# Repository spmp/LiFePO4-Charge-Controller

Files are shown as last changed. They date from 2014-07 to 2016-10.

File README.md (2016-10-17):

LiFePO4 Charge Controller
=========================

This is a rolling project to create a fully automatic
_LiFePO4_ battery charger for my, and possibly other 
battery packs based on the HP Blade power supply ESP-120.

Principal of operation
----------------------
LiFePO4 batteries have a relativly simple charging profile:

 * Charge at constant current up to a set voltage, usually 3.65Volts per cell
 * Turn off charging and rest the batteries for a given time
 * If you must, float the batteries at 3.45Vpc
 
Thanks to the efforts of a German group the ESP-120 is well
documented with a known and stable voltage control from 30-53V
with positive voltage into a trim-pot pin and 53-63 with a slight
negative voltage to this pin. There is an inverse relationship
between voltage at the pot, and the supplies output voltage.
~5Vin=> 30Vout, 0Vin=>53Vout.

To operate as a charger two of these units are connected
in series. This is easy as the DC output is isolated from
the case. To achieve constant current charging, the voltage of the
supplies is brought up slowly by modifying (decreasing) Vin 
whilst monitoring the current until the desired current is reached.
Vin is decreased to maintain this constant current until There
setpoint is reached, at which point the PSU's are turned off.

The PSU's are protected by a very large external diode (75A, 200V).

The planned itterations are as follows, with each mature
and completed iteration being moved into its appropriate 
folder upon completion:

Repo layout
-----------
```
.
├── code            Charge controller logic
│   └── AVR-lib     General AVR libraries. Should be a submodule
│       └── lib
├── doc             Documents relating to the ESP-120/HP3KW
├── pcb             Output PCB files
└── schematic       Schematic
```

The code is written in C using [Kdevelop] and built using [avr-gcc].

The schematic and PCB layout are done in [Kicad]

Current Implimentation
----------------------
Photos to come

Iterations:
------------
1.  **Mark I: Proof of concept using onboard**

    - Construction on breadboard
    - Powered off the PSU power GND - 12V via an LM7805, so has common ground with Cycle Analyst
    - shunt and differential opamp via built in 10bit ADC for current measurement
    - 100:1 resistor divider via 10bit ADC for output voltage measurement
    - Output is a PWM based 'DAC' to a fet/transistor between two pot's setting max/min voltage.
    - Output/input via isolated serial interface.
  
2.  **Mark II: further improvements**
    - Impliment isolated I2C to PSU controllers for PSON and current measurement.
    - Check PSU current VS shunt current, once verified they are the same with similar reliability, discontinue use of shunt.
    - Impliment software usart for Rx only to recieve SOC etc. from the cycle analyst
    - Assess whether external DAC's and ADC's are nescesarry.
    - Likely that external ADC will be, so use it.
    - Investigate and impliment different charging strategies.
    - LCD?
    - BMS integration
  
3.  **Mark III: Close to Final** 
    - PCB based, on its own board. 
    - Use specialised AVR with CAN support
    - Similar codebase to MarkII, trying to remove interrupt driven routines
    - Safety/Failsafe etc. much more error checking.
    - Impliment CAN somehow

Currently half way through Iteration 2. Soon BMS integration will be required, and maybe we will do CAN bus things then too. Maybe port to STM32.

### Mark I: Proof of concept using onboard, Design considerations

Inputs:
-------
 **Current:** 
   Current will be measured using the shunt resistor on the PSU's PCB.
   It has a resistance of 0.0002Ohm, and will require a diffrential opamp
   in order to amplify the signal to the 5V range. There is already an opamp
   on the PCB that does this, and it may be sufficient to use this.
   
   One 10bit ADC channel on the micro will do this, preferebly with the 
   1.25V internal reference.
   
   With a maximum current of say 60A, the finest measurement we can make is:
     60/1024 = 59mA
   which is sufficient.
   
 **Output Voltage**
   Output volatage will be measured by another 10bit ADC channel via a 100k:1k 
   resistor divider network.
   Using the internal 1.25 voltage reference, this gives a maximum measurable voltage of
   125V with an accuracy of 0.122, again, more than sufficient!
   (DAC RC calculator)[http://sim.okawa-denshi.jp/en/PWMtool.php]
   
Outputs:
--------
 **Vin:**
   Volatage between power ground and a pad from a reomoved potentiometer needs to 
   be adjusted from ~5V to 0V.
   
   In this implimentation we will use PWM driving a fet to ground on from the 5V supply rail
   with the pot pin in the middle, and a 330nF cap to ground.
   
 **Serial:**
   Debugging and logging will be via serial
   
 **LED's and stuff:**
   - Blinking light (things alive)
   - Charging
   - Complete
   - State of charge bar graph for in the window 8)
   - Even better would be EL wire or tape on the exterior.

[Kdevelop]: https://www.kdevelop.org/
[avr-gcc]: http://www.nongnu.org/avr-libc/
[kicad]: http://kicad-pcb.org/

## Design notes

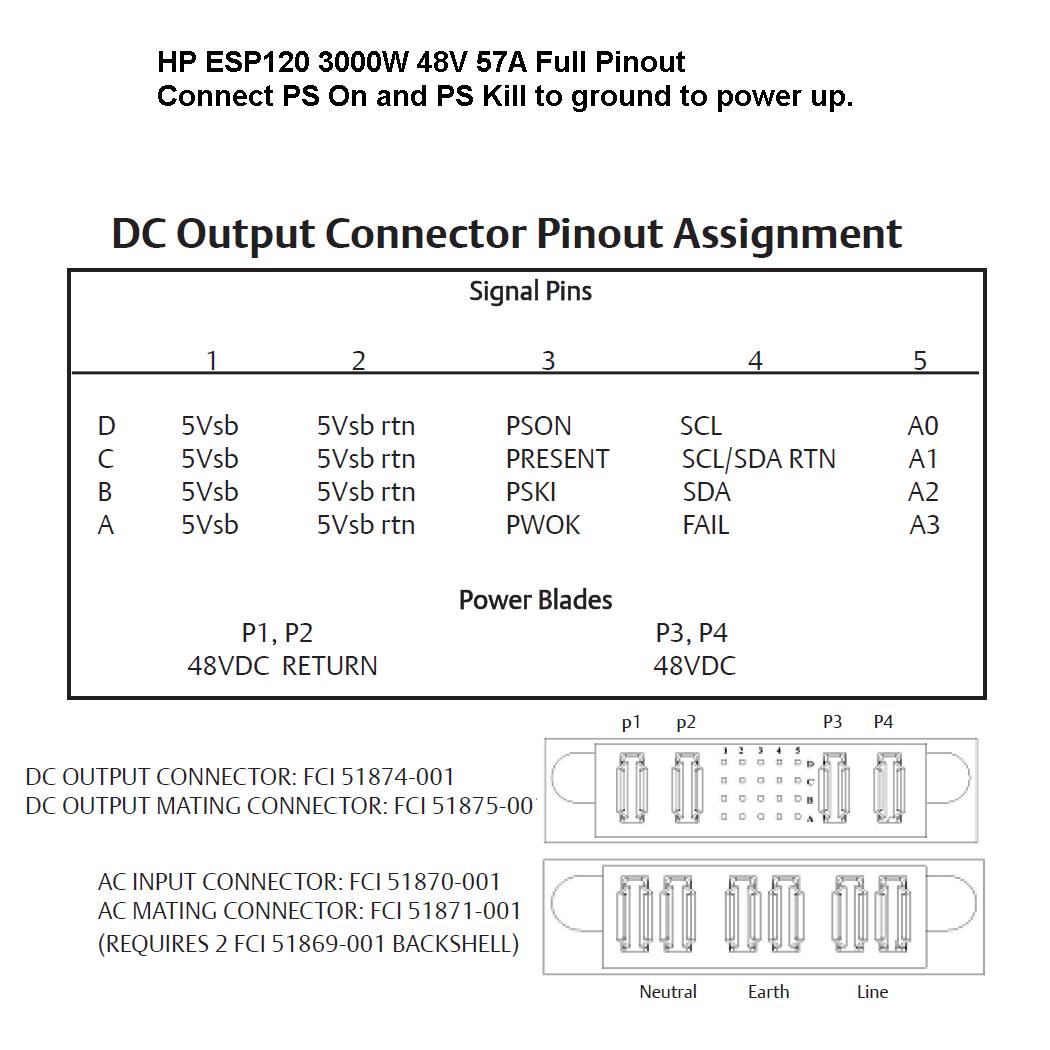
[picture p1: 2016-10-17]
doc/HP ESP120 Full pinout.jpg

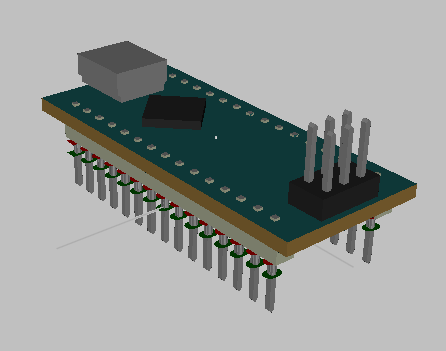
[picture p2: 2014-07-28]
schematic/arduino_nano.png

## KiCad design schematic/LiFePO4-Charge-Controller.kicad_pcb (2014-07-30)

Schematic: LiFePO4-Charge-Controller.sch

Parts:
CI1a1, CI1c1, CI2a1, CI2c1, CI3a1: 100nF
CI1b1, CI1d1, CI2b1, CI2d1, CI3b1: 1uF
CINA1: 100nF
CV1: 10pF
Cpwm1: 300nF
Dled1, Dled2: LED
OC1, OC2, OC3: PC817; DIP4
PI1, PI2, PI2C1: I2C
PIRS232: RS232
Popto1, Popto2, Popto3: opto
Pshunt1: differential
Pvolt1: Gnd PWM 12V B+
Qpnp1: NPN
RI1scl1, RI1sda1, RI2scl1, RI2sda1: 5k
RI2Cscl1, RI2Csda1: 1.8k
RVR1a1, RVR1b1: 99k
RVR2a1, RVR2b1: 1k
Rg1: 5k
Rled1: 1k
Rled2: 1K
Ropto1, Ropto2, Ropto3: 1k
Rpwm1: 120
RpwmDrv1: 560
UI1, UI2: SI8400; MODULE
UINA1: AD8236; MODULE
UIR1: SI8400; MODULE
UuC1: ARDUINO_Nano; DIL20

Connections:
5v: CI1a1.1, CI1b1.1, CI2a1.1, CI2b1.1, CI3a1.2, CI3b1.2, CINA1.1, PI2C1.1, RI2Cscl1.1, RI2Csda1.1, Rpwm1.2, UI1.8, UI2.8, UINA1.8 (+VS), UIR1.1, UuC1.12
D3: Ropto1.1, UuC1.21
D5: Ropto2.1, UuC1.23
D6: Ropto3.1, UuC1.24
Gnd: CI1a1.2, CI1b1.2, CI2a1.2, CI2b1.2, CI3a1.1, CI3b1.1, CINA1.2, CV1.2, Cpwm1.2, Dled1.2 (K), Dled2.2 (K), OC1.2, OC2.2, OC3.2, PI2C1.4, Pvolt1.4, Qpnp1.1 (E), RVR2a1.2, RVR2b1.2, UI1.5, UI2.5, UINA1.5 (-VS), UINA1.6 (REF), UIR1.4, UuC1.14, UuC1.19
I2C1_GND: CI1c1.2, CI1d1.2, PI1.4, UI1.4
I2C2_GND: CI2c1.2, CI2d1.2, PI2.4, UI2.4
unnamed: UIR1.2, UuC1.17
unnamed: UIR1.3, UuC1.16
unnamed: PI1.3, RI1scl1.2, UI1.3
unnamed: PI1.2, RI1sda1.2, UI1.2
unnamed: PI2.2, RI2sda1.2, UI2.2
unnamed: CV1.1, RVR1a1.2, RVR1b1.2, RVR2a1.1, RVR2b1.1, UuC1.4
unnamed: PIRS232.3, UIR1.6
unnamed: PIRS232.2, UIR1.7
unnamed: PIRS232.1, UIR1.8
unnamed: PI2.3, RI2scl1.2, UI2.3
unnamed: OC1.4, Popto1.1
unnamed: OC3.4, Popto3.1
unnamed: OC3.1, Ropto3.2
unnamed: OC2.3, Popto2.2 (PM)
unnamed: OC2.4, Popto2.1
unnamed: OC2.1, Ropto2.2
unnamed: OC1.3, Popto1.2 (PM)
unnamed: OC3.3, Popto3.2 (PM)
unnamed: OC1.1, Ropto1.2
unnamed: Cpwm1.1, Pvolt1.3, Qpnp1.3 (C), Rpwm1.1
unnamed: Qpnp1.2 (B), RpwmDrv1.2
unnamed: Dled1.1 (A), Rled1.2
unnamed: Dled2.1 (A), Rled2.2
unnamed: RpwmDrv1.1, UuC1.27
unnamed: Rled2.1, UuC1.30
unnamed: Rled1.1, UuC1.29
unnamed: Rg1.1, Rg1.2, UINA1.2 (RG)
unnamed: UINA1.7 (Vout), UuC1.5
unnamed: Pshunt1.2 (PM), UINA1.4 (+IN)
unnamed: Pshunt1.1, UINA1.1 (-IN)
unnamed: Rg1.3, UINA1.3 (RG)
unnamed: Pvolt1.2, UuC1.15
unnamed: CI2c1.1, CI2d1.1, PI2.1, RI2scl1.1, RI2sda1.1, UI2.1
unnamed: CI1c1.1, CI1d1.1, PI1.1, RI1scl1.1, RI1sda1.1, UI1.1
unnamed: PI2C1.3, RI2Csda1.2, UI1.7, UI2.7, UuC1.8
unnamed: PI2C1.2, RI2Cscl1.2, UI1.6, UI2.6, UuC1.9
unnamed: Pvolt1.1, RVR1a1.1, RVR1b1.1
RS232_GND: PIRS232.4, UIR1.5

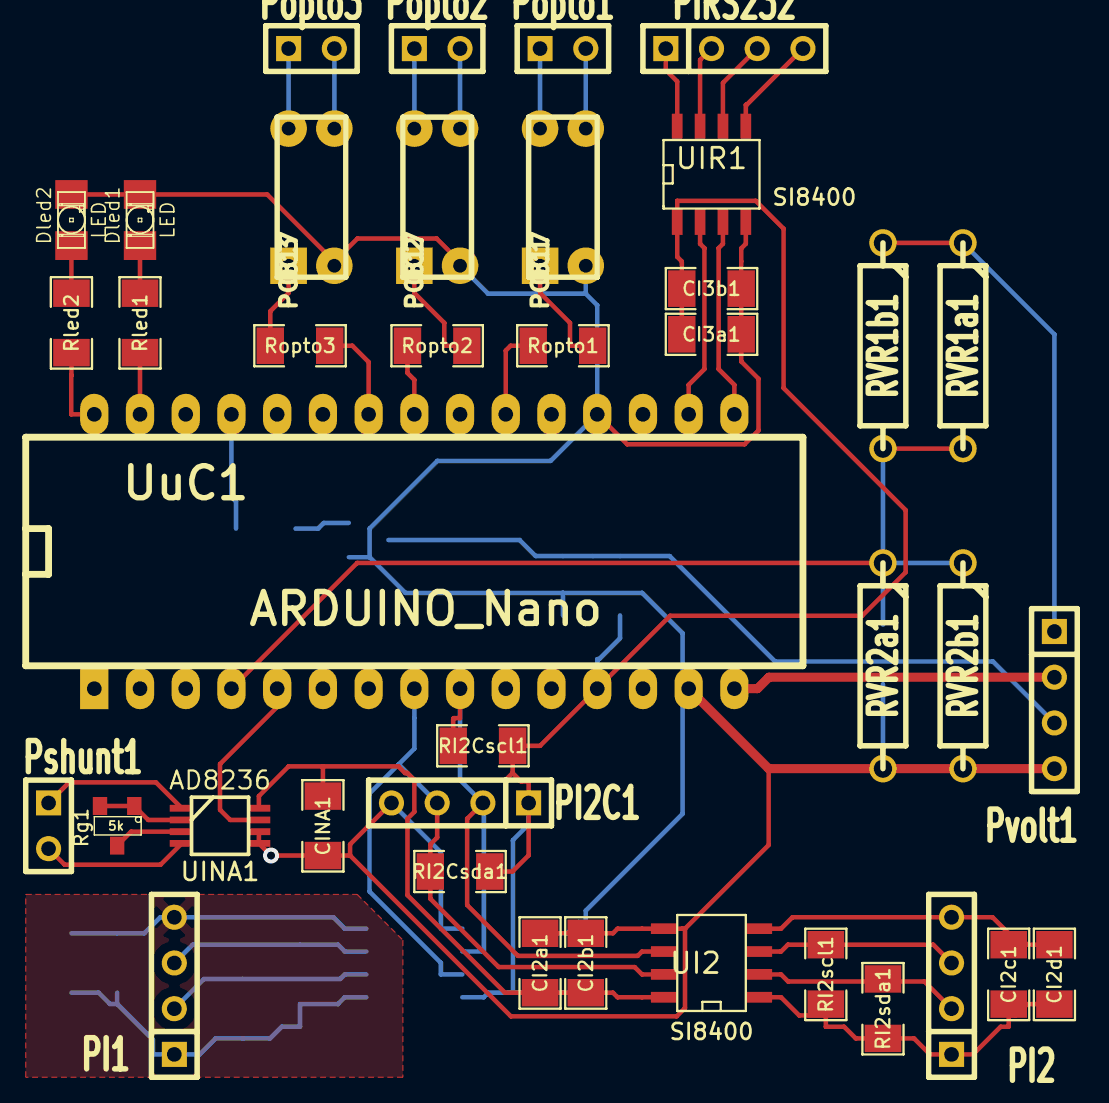
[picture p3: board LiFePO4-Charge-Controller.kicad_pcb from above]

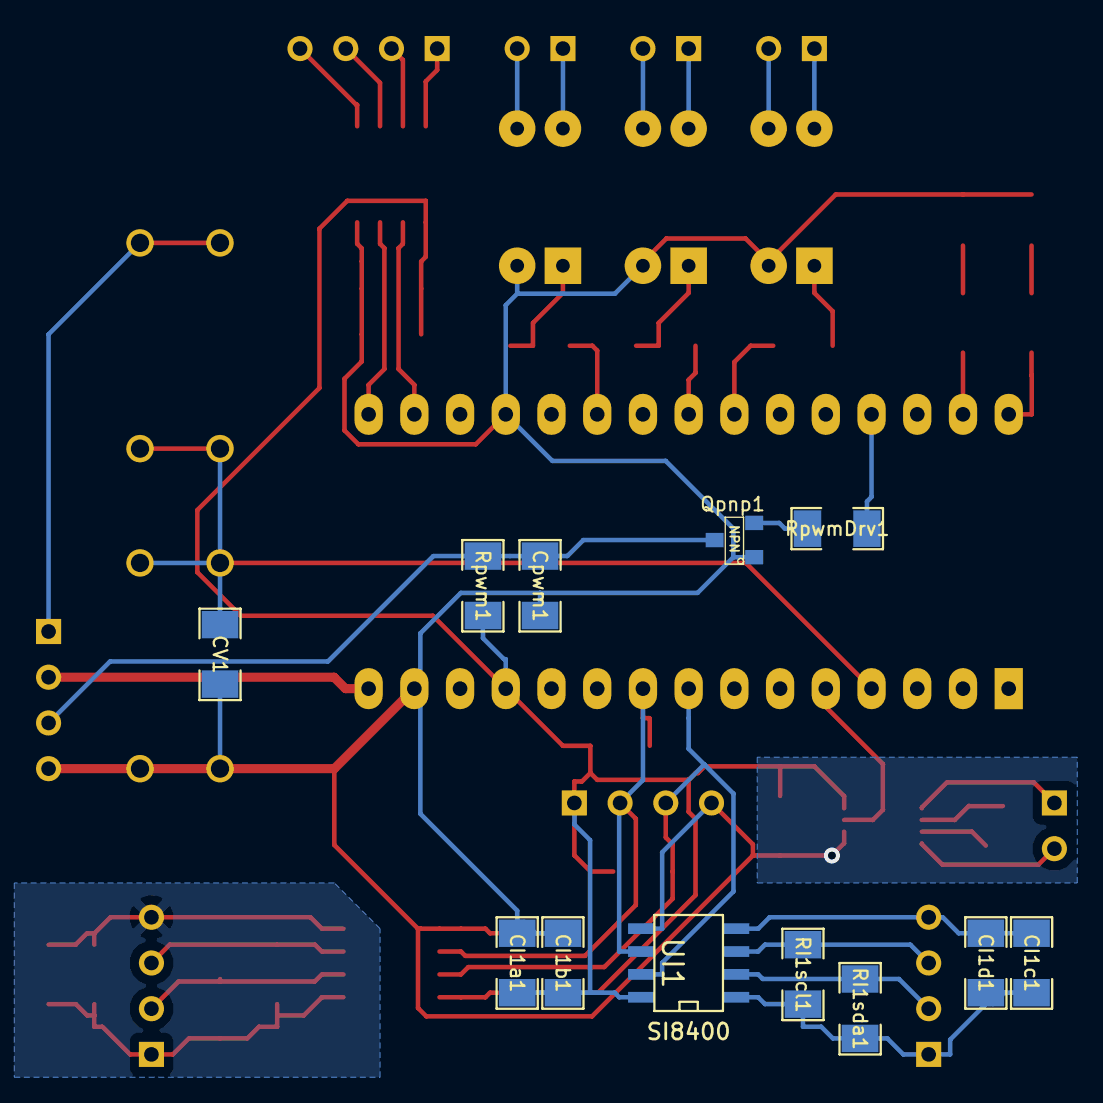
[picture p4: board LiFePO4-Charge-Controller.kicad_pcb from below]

Board: 2 copper layers, 51 parts (12 on the bottom side), 45 nets.

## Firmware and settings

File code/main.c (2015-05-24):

#include <avr/io.h>
#include <avr/interrupt.h>
#include <avr/sleep.h>
#include <util/delay.h>

#include "hardware.h"
#include "AVR-lib/wd.h"
#include "process-control.h"
#include "command.h"
#include "log.h"
#include "AVR-lib/usart.h"

// Watchdog and reset state.
// "You're not suppose to call get_mcusr() in main().
// "the attribute section(".init3") puts the code in before main() so it runs automatically before entering main().
// NOTE: This code will work with a recent version of 'optiboot' as the bootloader:
uint8_t resetFlags __attribute__ ((section(".noinit")));
void resetFlagsInit(void) __attribute__ ((naked)) __attribute__ ((section (".init0")));
void resetFlagsInit(void)
{
  // save the reset flags passed from the bootloader
  __asm__ __volatile__ ("mov %0, r2\n" : "=r" (resetFlags) :);
}


/**
 * @var send_log, whether to log to USART or not
 **/
uint8_t send_log = 0;

/**
 * @brief function to be called from the once per second clock ISR
 * 
 * Activates the log send
 * Toggles the LED
 **/
void once_per_second() {
    send_log = 1;
    PORTB ^= (1 << PORTB5); //Toggle LED
    PORTB ^= (1 << GREEN_LED); //Toggle Green LED
    PORTB ^= (1 << RED_LED); //Toggle Red LED
}

// #undef MEDIUM_TIME_INTERVAL
// #define MEDIUM_TIME_INTERVAL 15
void medium_timestep() {
//     send_log = 1;
    begin_process_control_flag = 1;
}

void fast_timestep() {
    send_log = 1;
    begin_process_control_flag = 1;
}

int main() {
    cli();
    set_sleep_mode(SLEEP_MODE_IDLE);
    init_hardware();
//     init_PID(&process);
    sei();
    
    //Send initialisation message:
    // TODO: This will show how many resets... after the R
    send_string_p(PSTR("Rx LiFePO4 Charge Controller for ESP-120 PSU's. V:0.2.0. Jasper Aorangi 2014. Have a nice day 8): "));
    send_uint16(resetFlags);
    send_string_p(PSTR(" x\r\n"));
    
    //Set timer callbacks
    clock_set_seconds_callback(&once_per_second);
    clock_set_medium_time_callback(&medium_timestep);
//     clock_set_fast_time_callback(&fast_timestep);
    
    //USART line handler
    usart_set_handle_char_string_from_serial(&handle_line);
    
    
    //Pre Process Control Wait and checks -- Cannot wait more than Watchdog reset
    uint8_t i;
    for (i=0; i <= PSU_WAIT_ON; i++)
    {
        _delay_ms(1000);             //Wait for PSU to be ready NOTE:WE Want this happening IN whilst process control can check stuff!!!
        wd_reset();
    }
    process_control_enable();           //Enable Process Control
    PIDtype = 1;                        //Enable temporary current control programme.
    
    for (;;) {
        sleep_mode(); // blocked until after an interrupt has fired
        
        //USART
        while (num_in_serial_buffer()) { //check whether there is anything on the serial buffer, if there is, look at it
            handle_single_char_from_serial();
        }
        
        //Process Controll
        if ( begin_process_control_flag ) {
            begin_process_control_flag = 0;
            process_control(&process);
        }
        
        //Logging
        if (send_log) {
            send_log = 0;
            log_to_serial(&process);
        }
        wd_reset();
    }

    return 0;
}

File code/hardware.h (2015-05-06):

/*This file has been prepared for Doxygen automatic documentation generation.*/
/** 
 * @file hardware.h
 *
 * @brief Header for Hardware.c, setting up project specific Hardware
 *
 * - Compiler:          gcc-avr
 * - Project:           LiFePO4 Charge Controller
 * - uC                 AVR Mega328p on Arduino Nano board
 * 
 * @author               Jasper Aorangi
 * @Date: July 2014
 *****************************************************************************/

#pragma once
#include <avr/io.h>
#include "AVR-lib/adc.h"
#include "AVR-lib/i2c_safe.h"
#include "AVR-lib/usart.h"
#include "AVR-lib/timers.h"
#include "process-control.h"
#include "esp120.h"
#include "AVR-lib/wd.h"

/** 
 * This header/c file together setup the project specific hardware and resources
 * 
 * Hardware Description:
 *  The basic unit is an Arduino Nano, an AT Mega 328p
 *  
 *  Inputs
 *      Current sensing, either by I2C or ADC from shunt+IN-AMP
 *          @resource ADC, internal 10bit
 *              OR
 *          @resource I2C, to powersupply 1 and/or two
 *          @resource PC5, I2C SCL
 *          @resource PC4, I2C SDA
 *              @I2Caddress 0xA0
 *                  ... to ...
 *              @I2Caddress 0xAE
 *          @var current, uint16, mA
 *      Voltage sensing via a 100:1 divider with zener protection to int. ADC
 *          @resource ADC0/PC0, internal 10bit, 1.1Vref, giving resolution of 0.11V (Arduino Nano A0)
 *          @var voltage, uint16, mV
 *              OR
 *          @resource I2C, to 16bit ADC
 *          @resource PC5, I2C SCL
 *          @resource PC4, I2C SDA
 *              @I2Caddress 0xF4628, or (0xF4629,32,33)
 *      Switches
 *          @resource ???
 *  Outputs:
 *      Heartbeat
 *          @resource Timer/Counter2, Clock heartbeat
 *          @resource PB5, on board LED
 *      Voltage to the PSU voltage set pin. PWM to RC-network
 *          @resource Timer/Counter1, in PWM mode 8
 *          @resource OC1A/PB1 (Arduino Nano D9)
 *          @var duty, uint16, PWM duty cyle
 *      Serial input outuput
 *          @resource USART
 *          @resource PD0, Rx
 *          @resource PD1, Tx
 *      Serial, software serial Rx for Cycle analyst input.
 *          @resource ???
 **/

/** Outupt type defines: **/
#define ABSOLUTE        0       // Absolute value of variable under inspection
#define PERCENT         1       // Percentage*100

/** PWM Channel names **/
#define PWM_CHAN_A      0
#define PWM_CHAN_B      1

/* Project specific defines */
#define USART_BAUDE     38400   //Highest stable Baude at 16MhZ FCPU
#define I2C_FREQ        50000  //Limit for the HP PSU
#define PWM_TOP         0xFFF  // PWM TOP value, 12bit. Such that PWM Frequency is ClockSpeed(16Mhz)/(2*Prescaler(1)*TOP) = 1.953kHz
#define PWM_START       0xFFF-1 // Which value to start the PWM at on powerup from cold 
#define DESIGN_SOC      8960    // System design State of Charge in Ah

#define PSU_WAIT_ON     10      //Time in seconds from PSU power on to output ready

/* Hardware specific defines: */
#define ONBOARD_LEDPort PORTB
#define ONBOARD_LED_DriectionReg    DDRB
#define ONBOARD_LED     PB5

#define GREEN_LED       PB4
#define RED_LED         PB3

#define PSU_ON_PORT     PORTD
#define PSU1_ON         PD3
#define PSU2_ON         PD5

#define VsensePort      PORTC
#define VsensePin       PC0
#define VsenseADC       ADC0
#define VenseADC_REF    VREF_INTERNAL

#define PSU1_ADDRESS    24
#define PSU2_ADDRESS    24

/**
 * @struct PSU_state, The state PSU's 1 and 2 from I2C data
 **/
struct PSU_state {
    uint16_t PSU1_current;      // PSU1 current
    uint16_t PSU1_temperature;  // PSU1 Temperature
    uint16_t PSU1_line_voltage; // PSU1 Line voltage
    uint8_t  PSU1_PSON_state;   // PSU1 power status
    uint16_t PSU2_current;      // PSU2 current
    uint16_t PSU2_temperature;  // PSU2 Temperature
    uint16_t PSU2_line_voltage; // PSU2 Line voltage
    uint8_t  PSU2_PSON_state;   // PSU2 power status
};

/**
 * @brief Initialise hardware 
 * 
 * Initialise all hardware relevant to the project, usart, i2c, clock, external
 * sensors, Everyting!
 * One call to rule them all
 */
void init_hardware(void);

/**
 * @brief Initialise I/O ports
 * 
 * Initialise PIN I/O states that do not fall into the PWM, I2C/TWi etc categories
 */
void init_io_ports(void);

/**
 * The followng are functions abstacting measurements into internal values.
 **/

/**
 * @brief Get voltage measurement, taking into consideration protection diode drop
 * 
 * @return uint16, the corrected voltage in mV
 **/
uint16_t get_voltage( void );

/**
 * @brief Get the current flowing through the system
 * 
 * @return uint16, the current in A*100
 **/
uint16_t get_current( void );

/**
 * @brief Get the state of charge of the batteries
 * 
 * Gets the state of charge in Ah or percentage*100
 * @param type, see defines
 * @return uint16, the state of charge
 **/
uint16_t get_SoC( uint8_t op_type );
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

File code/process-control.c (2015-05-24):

/*This file has been prepared for Doxygen automatic documentation generation.*/
/** 
 * @file process-control.c
 *
 * @brief Variables and functions related to the state and controll of a process
 *
 * - Compiler:          gcc-avr
 * - Project:           LiFePO4 Charge Controller
 * - uC                 AVR Mega328p on Arduino Nano board
 * 
 * @author              Jasper Aorangi
 * @Date: July 2014
 *****************************************************************************/
#include "process-control.h"

/**
 * @brief Variables that control whether the process_control is able to run (again)
 * 
 * @var begin_process_control_flag
 * Flag that indicates that process should run
 * @var process_control_running_flag
 * Flag that indicates process_control is running
 * @var process_control_enable
 * Flag for global enable/disable of process_control
 **/
uint8_t PIDtype = 0;
uint16_t cPIDmaxread = 30000;

uint8_t begin_process_control_flag = 0;
uint8_t process_control_running_flag = 0;
uint8_t processControlEnable = 0;               //disabled by default

/**
 * @brief Variables used by the actual programmes running in calculate_outputs
 * 
 * @var setpoint_reached_counter
 * When the setpoint is reached start counting cycles that this is true
 * @var rest_count
 * How long have we been resting for. May be redundant if we decriment rest timer.
 * @var rest_init_flag
 * Allow us to run some stuff on the first rest
 * @var done_init_flag
 * Same as above
 * @def SETPOINT_REACHED_COUNT
 * How many counts of setpoint_reached_counter to count for
 * @def PWM_THRESHOLD_REDUCTION
 * How much to reduce the PWM by if we enounter an over threshold
 **/
#define SETPOINT_REACHED_COUNT      50
#define PWM_THRESHOLD_REDUCTION     1000
uint8_t setpoint_reached_counter = 0;
uint8_t rest_init_flag = 0;
uint8_t done_init_flag = 0;
uint8_t startPSUflag = 0;
uint32_t Ah_QuarterSecond = 0;

/** @brief struct(s) for PID **/
struct u_PID_DATA pidData_cc;    // PID data for constant current
struct u_PID_DATA pidData_cv;    // PID data for constant voltage
// = {   // PID data for constant voltage

/** @brief struct PSU_state psu_state for storing PSU data **/
struct PSU_state psu_state = {0};

/** @brief struct Process process for program 1 **/
struct Process process = {
    {0},
    {
    .pwm_duty = PWM_START,          // Duty cycle of pwm_duty
    .PSU_state = 20,         // State of the PSU's
    .Ah_count = 0,          // How many Ah's have passed through the charger in this cycle
    .charge_timer = 0,      // How long have we been in the 'bulk' charging phase
    .cur_rest_time = 0,     // How long have we been resting?
    .rest_timer = 0,        // How long do we need to rest for?
    .float_timer = 0,        // How long do we need to float charge?
    .charge_state = 0,      // State of charging, Bulk, rest, float, Done
    .error_code = 0,         // Code of error that is encounted, will be set and cleared regularily - needs to be writtne to EEPROM somewhere
    .charge_progress = 0    // Percentage of charging done.
    },
    {
    .program_number = 1,     // An index for the process, such that process_control knows with process to run.
    .current_max = 35000,     // Absolute maximum current. Shutdown if over
    .current_threhold = 3500,// Current at which to try to recover over current condition, needs to be lower than current_max and above current_charge
    .current_charge = 30000, // Current to charge the batteries at
    .current_float = 20000, // Max current for float charge
    .voltage_max = 1037,    // Absolute maximum battery voltage. Shutdown if over
    .voltage_min = 8300,       // Minimum battery voltage. Error or batteries disconnected if under.
    .voltage_threshold = 1035, // Voltage at which to try to recover over voltage condition, needs to be lower than voltage_max and above voltage_charged
    .voltage_charged = 1013, // Voltage at which to stop bulk charging
    .voltage_float = 942,   // Voltage at which to float the batteries
    .rest_time = 36,         // Time between charged voltage and driving or float/done. This is in seconds per Ah
    .max_PSU_temp = 70,      // Maximum temperature for any PSU before shutdown
    .max_PSU_volt = 300,     // Maximum PSU line voltage
    .min_PSU_volt = 200,     // Minimum PSU voltage
    .max_battery_temp = 50,  // Maximum temperature of any battery before shutdown.
    /** PID **/
    .PIDoutput = 0,          // Output from the PID algorythm
    .cc_P_Factor = 1,        //! The cc Proportional tuning constant, multiplied with SCALING_FACTOR
    .cc_I_Factor = 0,        //! The cc Integral tuning constant, multiplied with SCALING_FACTOR
    .cc_D_Factor = 0,        //! The cc Derivative tuning constant, multiplied with SCALING_FACTOR
    .cv_P_Factor = 3,        //! The cv Proportional tuning constant, multiplied with SCALING_FACTOR
    .cv_I_Factor = 0,        //! The cv Integral tuning constant, multiplied with SCALING_FACTOR
    .cv_D_Factor = 3         //! The cv Derivative tuning constant, multiplied with SCALING_FACTOR
    }
};

/** 
 * @brief Initialise the PID from Process struct
 * @param *process, a struct of type Process in which get the pid initialisation variables
 **/
// void init_PID(struct Process *process)
// {
//     struct Settings *settings = &process->settings;
//     u_pid_Init(settings->cc_P_Factor * SCALING_FACTOR, settings->cc_I_Factor * SCALING_FACTOR, settings->cc_D_Factor * SCALING_FACTOR, &pidData_cc);
//     u_pid_Init(settings->cv_P_Factor * SCALING_FACTOR, settings->cv_I_Factor * SCALING_FACTOR, settings->cv_D_Factor * SCALING_FACTOR, &pidData_cv);
// }

/**
 * @brief Get the state of the system, input values and output states
 * 
 * @param *process, a struct of type Process in which to save the system state
 **/
void get_state(struct Process *process) {
    struct Inputs *inputs = &process->inputs;
    struct Outputs *outputs = &process->outputs;
    
    // Get the external states
    get_psu_state(inputs);
    inputs->current = (double)inputs->PSU1AnalogData.Current*1.2057067147 + 1811.45;
    inputs->voltage = get_voltage();
    
    //Calculate Amp Hours assuming readings every 4th of a second
    //Ah_QuarterSecond += inputs->current;
    outputs->Ah_count += inputs->current/(60*60*10*4);
    
// //     inputs->current = (psu_state.PSU1_current+psu_state.PSU1_current)/2;
    
    // Get the internal states
// //     outputs->pwm_duty = get_pwm_duty(PWM_CHAN_A, ABSOLUTE);
//     outputs->charge_progress = get_SoC(ABSOLUTE);
}

/**
 * @brief Calculate the outputs in order to controll the process
 * 
 * Details are elsewhere and in code.
 * 
 * @param *process, a struct of type Process in which to save the system state
 **/
void calculate_outputs(struct Process* process)
{
    
    struct Inputs *inputs = &process->inputs;
    struct Outputs *outputs = &process->outputs;
    struct Settings *settings = &process->settings;
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

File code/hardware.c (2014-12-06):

/*This file has been prepared for Doxygen automatic documentation generation.*/
/** 
 * @file hardware.c
 *
 * @brief Header for Hardware.c, setting up project specific Hardware
 *
 * - Compiler:          gcc-avr
 * - Project:           LiFePO4 Charge Controller
 * - uC                 AVR Mega328p on Arduino Nano board
 * 
 * @author               Jasper Aorangi
 * @Date: July 2014
 *****************************************************************************/
#include "hardware.h"

//Initialise the PSU_state
// struct PSU_state psu_state = {0};


/**
 * @brief Initialise hardware 
 * 
 * Initialise all hardware relevant to the project, usart, i2c, clock, external
 * sensors, Everyting!
 * One call to rule them all
 */
void init_hardware(void ) {
    wd_reset();
    WD_SET(WD_OFF);
    init_clock();
    init_io_ports();
    init_usart(USART_BAUDE, F_CPU);
    i2c_init(I2C_FREQ,F_CPU);
    init_pwm(PWM_TOP, 1);
    set_pwm(1,PWM_START);
    WD_SET(WD_RST,WDTO_4S);
    //Set B1 as output
//     DDRB |= (1 << PIN1);
}

/**
 * @brief Initialise I/O ports
 * 
 * Initialise PIN I/O states that do not fall into the PWM, I2C/TWi etc categories
 */
void init_io_ports(void ) {

    //Set Internal LED pin to output
    DDRB |= (1 << ONBOARD_LED);
    //Set Green LED pin to output
    DDRB |= (1 << GREEN_LED);
    //Set Red LED pin to output
    DDRB |= (1 << RED_LED);
    
    //Set PSU1_ON pin to output
    DDRD |= (1 << PSU1_ON);
    //Set PSU2_ON pin to output
    DDRD |= (1 << PSU2_ON);
    
    //Set outputs OFF
    PORTD &= ~((1 << PSU1_ON) | (1 << PSU2_ON));
    //Set Green LED ON
    PORTB |= (1 << GREEN_LED);

}

/**
 * The followng are functions abstacting measurements into internal values.
 **/

/**
 * @brief Get voltage measurement, taking into consideration protection diode drop
 * 
 * @return uint16, the corrected voltage in mV
 **/
uint16_t get_voltage( void )
{
//     return read_ADC_pin_millivolts(0, VREF_INTERNAL);
    return read_ADC_pin_millivolts(0, VenseADC_REF);
}

/**
 * @brief Get the current flowing through the system
 * 
 * @return uint16, the current in A*100
 **/
uint16_t get_current( void )
{
    return 20000;
}


/**
 * @brief Get the state of charge of the batteries
 * 
 * Gets the state of charge in Ah or percentage*100
 * @var type, see defines
 * @return uint16, the state of charge
 **/
uint16_t get_SoC( uint8_t op_type )
{
    uint16_t soc = 531;
    
    if (!op_type){
        return soc;
    }
    else {
        return ((uint32_t)soc*100)/DESIGN_SOC;
    }
}

/**
 * @brief Get the PWM duty cycle
 * 
 * @var type, see defines
 * @return uint16, the pwm duty cycle
 **/
uint16_t get_pwm_duty( uint8_t pwm_chan, uint8_t op_type )
{
    if (!pwm_chan){
        if (!op_type){
            return OCR1A;
        }
        else {
            return ((uint32_t)OCR1A*10000)/PWM_TOP;
        }
    }
    else {
        if (!op_type){
            return OCR1B;
        }
        else {
            return ((uint32_t)OCR1B*10000)/PWM_TOP;
        }
    }
}


/**
 * @brief Get the state of the PSUs via I2C
 * 
 * @param psu_struct, struct PSU_state, struct in which to store the PSU's states
 **/
void get_psu_state(struct Inputs *ProcessControlInputs)
{
    //TODO: PSU State
    esp120_analog_data(PSU1_ADDRESS, &ProcessControlInputs->PSU1AnalogData);
//     *ProcessControlInputs->PSU1StatusReg = esp120_get_status_register(PSU1_ADDRESS);
//     esp120_analog_data(PSU2_ADDRESS, &ProcessControlInputs->PSU2AnalogData);
//     *ProcessControlInputs->PSU2StatusReg = esp120_get_status_register(PSU2_ADDRESS);
}

/**
 * @brief Get PSU's current
 * 
 * @param psu_number, the number 1 or 2 of the PSU
 **/
uint16_t get_psu_current( uint8_t psu_number, struct PSU_state *psu_struct)
{
    if (psu_number == 2 ) {
        return psu_struct->PSU2_current;
    }
    else {
        return  psu_struct->PSU1_current;
    }
}

/**
 * @brief Get PSU's voltage
 * 
 * @param psu_number, the number 1 or 2 of the PSU
 **/
uint16_t get_psu_line_voltage( uint8_t psu_number, struct PSU_state *psu_struct)
{
    if (psu_number == 2 ) {
        return psu_struct->PSU2_line_voltage;
    }
    else {
        return  psu_struct->PSU1_line_voltage;
    }
}

/**
 * @brief Get PSU's temperature
 * 
 * @param psu_number, the number 1 or 2 of the PSU
 **/
uint16_t get_psu_temperature( uint8_t psu_number, struct PSU_state *psu_struct)
{
    if (psu_number == 2 ) {
        return psu_struct->PSU2_temperature;
    }
    else {
        return  psu_struct->PSU1_temperature;
    }
}


/**
 * @brief Power on or off a PSU
 * 
 * @param psu_number, the number 1 or 2 of the PSU. Anything else (0,3,4..) does both
 * @param state, 0 turn off, 1 turn on, other turn off
 **/
void psu_power(uint8_t psu_number, uint8_t state)
{
    //Send the I2R command to turn the PSU on
    if (psu_number == 1 ) {
        if (state == 1) {
            //turn on
            PSU_ON_PORT |= (1 << PSU1_ON);
        }
        else {
            //turn off
            PSU_ON_PORT &= ~(1 << PSU1_ON);
        }
    }
    //Send the I2R command to turn the PSU on
    else if (psu_number == 2 ) {
        if (state == 1) {
            //turn on
            PSU_ON_PORT |= (1 << PSU2_ON);
        }
        else {
            //turn off
            PSU_ON_PORT &= ~(1 << PSU2_ON);
        }
    }
    else {
        if (state == 1 ){
            //turn on both PSU's
            PSU_ON_PORT |= ((1 << PSU1_ON) | (1 << PSU2_ON));
        }
        else {
            //turn off both PSU's
            PSU_ON_PORT &= ~((1 << PSU1_ON) | (1 << PSU2_ON));
        }
    }
}

/**
 * @brief Check the power state of a PSU in realtime.
 * 
 * @param psu_number, the number 1 or 2 of the PSU
 * @param state, 0 turn off, 1 turn on, other turn off
 **/
uint8_t psu_power_check(uint8_t psu_number)
{
    //Send the I2R command to check psu state
    if (psu_number == 1 ) {
        //check state
        return 0;
    }
    //Send the I2R command to turn the PSU on
    if (psu_number == 2 ) {
        //check state
        return 0;
    }
}

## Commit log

2014-07-22 Working code with basic USART interaction for checking voltage and setting PWM. NOTE: PWM as DAC use series 130 ohm (using 330 ohm) reistor with 10uF cap to ground as output
2014-07-22 getting ready for PID
2014-07-23 A fairly stable oscillating system thingee
    [command.c, main.c, process-control.c]
2014-07-24 process_control.c, calculate_outputs, notchargin case 0 done as far as can be expected with no real hardware to work on
2014-07-24 process_control.c, calculate_outputs, Bulk charge case 1 done as far as can be expected with no real hardware to work on
2014-07-28 Begin schematic and PCB, making account for multiple posibilities... oh joy. TODO: Reverse order of PID and pwm reduction to be inverted
    [LiFePO4-Charge-Controller.kicad_pcb, LiFePO4-Charge-Controller.sch, LiFePO4-Charge-Controller_before-opto.sch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]
2014-07-29 Autoraouted board b4 contraction
    [LiFePO4-Charge-Controller.dsn, LiFePO4-Charge-Controller.kicad_pcb, LiFePO4-Charge-Controller.sch]
2014-07-29 Smaller, w solid fill
    [LiFePO4-Charge-Controller.dsn, LiFePO4-Charge-Controller.kicad_pcb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]
2014-07-29 PCB satisfactory, bit of a mess around I2C, but will go with it
    [LiFePO4-Charge-Controller-B_Cu.gbl, LiFePO4-Charge-Controller-B_Mask.gbs, LiFePO4-Charge-Controller-B_Paste.gbp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]
2014-07-30 PWM/PID code corrected. PCB: In-Amp pad (module) corrected. Board done.
    [LiFePO4-Charge-Controller-B_Cu.gbl, LiFePO4-Charge-Controller-B_Mask.gbs, LiFePO4-Charge-Controller-B_Paste.gbp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]
2014-08-15 moving to another computer. PCB: Moving to new version of Kicad, and making resistors SMD etc
    [LiFePO4-Charge-Controller.sch]
2014-10-19 Modified schematic to incorporate fix on PWM output, still working on non tracked test code
    [LiFePO4-Charge-Controller.sch]
2014-12-06 Basic working solution
    [LiFePO4-Charge-Controller.sch]
2014-12-06 Further corrections from merge
    [command.c, command.h, hardware.h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]
2015-05-05 modified for new I2C address. Having issues with I2C reset and continue
    [command.c, hardware.h, process-control.c]
2015-05-06 I2C adress modified again for more robust adressing (hardware)
2015-05-23 Completing code for PIDtype 2 and 3: Wait timer and float timer
2015-05-23 fixing more code... not working somehow
    [command.c, process-control.c]
2015-05-23 Fixed PIDtype 2 problems. Fixed commands to return value on null input. Fixed Ah count.
    [command.c, process-control.c]
2015-05-23 Getting closer to float charge. Need current and voltage control
2015-05-23 Fixed Float pwm problem by adding float current control - Needs verification. Added limits detection and correction (stop all)
    [main.c, process-control.c]
2015-05-24 Fixed float. made logging nice.
    [main.c, process-control.c]
2015-05-24 Fix indenting and change logging order
    [process-control.c]
